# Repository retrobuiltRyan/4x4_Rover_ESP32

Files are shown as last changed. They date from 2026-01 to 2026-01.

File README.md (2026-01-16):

# 4x4_Rover_ESP32
Video is a great overview of capabilites and features.<br>
Watch the video (https://youtu.be/ucYs9Jp9uSM)

gif

Generic platform for 1:10 scale robot rover (skid steer style) with ESP32 and PS4 controller.  Hardware [mostly] from scratch. The 1:10 scale (primarily wheel span and chassis width) mimics some common RC and toy-scale bodies. Makes a uniquie sleeper build that can share a body from off-the-shelf kids toys. PCB has enough functionality to expand into complex robots.
render and real side by side

paa1gcam

PCB can control up to 6 DC motors and 8 Servo Motors. 
PCB render features

## CAD Project (View only) Feel free remix!
[4x4 Rover CAD](https://cad.onshape.com/documents/4f9534eae9bdb33bcf172fe9/w/a4954ea2d6d5d21b33e1d9c4/e/6819e643c891bac21c58d472) (Make a free onShape account to copy and edit)

## 🔩 Mechanical Hardware/Fasteners for Assembly (BoM)
| Item | Assembly | Description | Qty | Cost | Line Total | Vendor Link / McMaster Part# |
|---|---|---|-----|---|---|---|
| 1 | Wheel | Lego "Compatible" Tire 94x38 (or similar)  | 1 | $17.65 | $17.65 | [Link](https://www.aliexpress.us/item/3256808684598937.html) |
| 2 | Drive | Shaft Coupler, 4mm dia | 4 | $1.65  | $6.60 | [Link](https://www.aliexpress.us/item/3256805863207590.html) |
| 3 | Drive | Motor 12V, 82 RPM | 4 | $5.74  | $22.96 | [Link](https://www.aliexpress.us/item/3256807500148966.html) or [Link](https://www.aliexpress.us/item/3256807350691232.html) |
| alt3 | Drive | Motor 12V, 82 RPM + RC Wheel | 4 | $6.46  | $25.84 | [Link](https://www.aliexpress.us/item/3256806026937992.html) |
| 5 | Chassis | #6-32 x 0.5 in Round Head Screw | 28  | $0.03  | $0.94 | 90279A148 |
| 6 | Chassis | #6-32 x 0.75 in Round Head Screw | 20  | $0.04  | $0.83 | 90279A151 |
| 7 | Chassis | #6-32 nut | 20  | $0.02  | $0.40 | 90480A007 |
| 8 | Chassis | #6-32 nylon lock nut | 20  | $0.04  | $0.80 | 99397A622 |
| 9 | Chassis | #6-32 x 1.0 in F/F Hex Standoff (optional) | 4 | $0.47  | $1.88 | 90480A005 |
| 10 | Wheel | #4-40 x 0.5 in Round Head Screw | 16  | $0.02  | $0.32 | 90272A110 |
| 11 | Wheel | #4-40 nut | 16  | $0.01  | $0.16 | 90480A005 |
| 12 | Wheel | #4-40 lock nut (optional) | 16  | $0.03  | $0.48 | 90631A005 |
| 13 | On/Off switch | Switch, SPST | 1 | $0.71  | $0.71 | [Link](https://www.digikey.com/en/products/detail/e-switch/RA11131121/2720267) |
| 14 | 3D Print Parts| PLA Filament (or whatever) | ~650g |$0.02/g | $13 | any | 
| | | | | | **$66.74** | Alternate hardware not included in total cost |

### Optional Forklift Assembly Motors + Parts. *Not a comprehensive list- just the essentials*
| Item | Assembly | Description | Qty | Cost | Line Total | Vendor Link / McMaster Part# |
|---|---|---|-----|---|---|---|
| 15 |Forklift |Motor High Torque 12V, 50RPM, (37mm dia) |  1  | $14 | $14 | [Amazon](https://www.amazon.com/dp/B07K9KPDNV) or [AliExpress](https://www.aliexpress.us/item/2251832401105488.html) |
|16 |Forklift | Flange Coupler 6mm | 1 |$2 | $2 |  [AliExpress](https://www.aliexpress.us/item/3256805863207590.html?) |
| 17 |Forklift |Motor (Linear Actuator ) 12V 50mm-stroke 15mm/s 64N | 2 | $22 | $44 | [AliExpress](https://www.aliexpress.us/item/3256808499012288.html) |
| 18 |Forklift |Bearing 625ZZ , 16mm OD dia, (5x16x5mm) | 8 |$0.55 |$4.40 |[AliExpress](https://www.aliexpress.us/item/3256809469842556.html) |
| 19 |Forklift |Bearing, 11mm OD dia, (5x11x5mm) | 10  | $0.25  | $2.50 | [AliExpress](https://www.aliexpress.us/item/3256807482131308.html) | 

## 🪫 Electronics (Control and Drive PCB)
PS4 Controller (Renewed) https://www.amazon.com/dp/B07QD2HK7B/ref=dp_cr_wdg_tit_rfb  (subject to availability most of the time)
| Reference | Value | Qty | DigiKey P/N | Adafruit P/N | AliExpress | Line total Cost |
|---|---|-----|---|---|---|---|
| BZ1 | Buzzer_5V | 1 | 445-2525-1-ND |  |  | 0.62 |
| C1,C3,C4,C5,C7,C8,C9 | 0.1uF 50V | 7 | 1276-1068-1-ND |  |  | 0.91 |
| C6,C10,C11 | 0.22uF 50V CER | 3 | 445-2283-1-ND |  |  | 0.78 |
| C12,C13,C14 | 22uF 50V | 3 | 399-11438-1-ND |  |  | 1.05 |
| D1,D5,D10,D11 | LED | 4 | 1080-1419-1-ND |  |  | 0.84 |
| D6,D7,D8,D9 | WS2812B | 4 |  | 3094 |  | 0.64 |
| D12 | SMF15A | 1 | SMF15A-E3-08CT-ND |  |  | 0.13 |
| J1 | PINHD_1x2_Male | 1 | S1012EC-40-ND |  |  | 0.43 |
| J2,J12,J14,J16 | Screw_Terminal_4_P3.50mm | 4 | 732-691243110004-ND |  |  | 8.28 |
| J3,J15 | ServoPort_04 | 2 | S1012EC-40-ND |  |  | 0.86 |
| J4,J5,J8,J13 | Screw_Terminal_2_P3.50mm | 4 | 732-2747-ND |  |  | 3.16 |
| J9 | Barrel_Jack | 1 | EJ508A-ND |  |  | 1.22 |
| J17 | PINHD_1x3_Male | 1 |  |  |  | 0 |
| Q1 | MOSFET P-CH 30V 25A TO252 | 1 | 785-1106-1-ND |  |  | 1.43 |
| Q2 | MMBT2222A | 1 | MMBT2222ATPMSCT-ND |  |  | 0.1 |
| Q3 | AO3400A | 1 | 785-1000-1-ND |  |  | 0.46 |
| R1,R2,R4,R7,R8,R9, R10,R13,R18,R22, R36,R37,R38 | 10K | 12 | 311-10.0KFRCT-ND |  |  | 0.14 |
| R3,R6 | 100 | 2 | 311-100FRCT-ND |  |  | 0.2 |
| R5,R19,R20,R32 | 1K | 4 | 311-1.00KFRCT-ND |  |  | 0.44 |
| R16 | 220 | 1 | 311-220FRCT-ND |  |  | 0.1 |
| R17,R21 | 330 | 2 | 311-330FRCT-ND |  |  | 0.22 |
| R33 | 100k | 1 | 311-100KFRCT-ND |  |  | 0.1 |
| RN1,RN2,RN3 | 220 array | 3 | CAY16-201J4LFCT-ND |  |  | 0.3 |
| U1 | INA260 | 1 | 296-47777-1-ND |  |  | 5.52 |
| U2 | ESP32 | 1 | 1965-ESP32-DEVKITC-32UE-ND |  |  | 10 |
| U3 | PCA9685PW | 1 | 568-11925-1-ND |  |  | 3.04 |
| U4,U6,U9 | DRV8833 | 3 |  |  | [Link](https://www.aliexpress.us/item/3256806096142480.html) | 5.23 |
| U5 | UCC27511ADBV | 1 | 296-49474-1-ND |  |  | 1.13 |
| U7 | L7812 | 1 | 296-44522-1-ND |  |  | 1.81 |
| U8 | IMU LSM6DS3TR-C | 1 |  | 4503 |  | 9.95 |
| U14 | MAX40200AUK | 1 | 175-MAX40203AUK+TCT-ND |  |  | 1.75 |
| U15 | L7805 | 1 | 497-7255-1-ND |  |  | 0.84 |
| U18,U19 | MP1584 Buck Module | 2 |  |  | [Link](https://www.aliexpress.us/item/3256806890547813.html) | 1.06 |
| - | PCB | 1 |  |  |  | 1 |
|  |  | |  |  | Total | **$63.74** |

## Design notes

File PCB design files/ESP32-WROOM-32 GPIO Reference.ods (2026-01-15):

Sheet: GPIO Reference
 | ESP32-WROOM-32 GPIO Reference
GPIO | Input | Output | Notes
0 | pulled up | OK | outputs PWM signal at boot, must be LOW to enter flashing mode
1 | TX pin | OK | debug output at boot
2 | OK | OK | connected to on-board LED, must be left floating or LOW to enter flashing mode
3 | OK | RX pin | HIGH at boot
4 | OK | OK
5 | OK | OK | outputs PWM signal at boot, strapping pin
6 | x | x | connected to the integrated SPI flash
7 | x | x | connected to the integrated SPI flash
8 | x | x | connected to the integrated SPI flash
9 | x | x | connected to the integrated SPI flash
10 | x | x | connected to the integrated SPI flash
11 | x | x | connected to the integrated SPI flash
12 | OK | OK | boot fails if pulled high, strapping pin
13 | OK | OK
14 | OK | OK | outputs PWM signal at boot
15 | OK | OK | outputs PWM signal at boot, strapping pin
16 | OK | OK
17 | OK | OK
18 | OK | OK
19 | OK | OK
21 | OK | OK
22 | OK | OK
23 | OK | OK
25 | OK | OK
26 | OK | OK
27 | OK | OK
32 | OK | OK
33 | OK | OK
34 | OK | x | input only
35 | OK | x | input only
36 | OK | x | input only
39 | OK | x | input only

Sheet: IoT Playgnd Pin assignments
 | ESP32-WROOM-32UE GPIO Reference
GPIO | Input | Output | Notes | 4x4 Rover Use | Notes
0 | pulled up | OK | outputs PWM signal at boot, must be LOW to enter flashing mode | enable for 3.3 regulator?
1 | TX pin | OK | debug output at boot | not used
2 | OK | OK | connected to on-board LED, must be left floating or LOW to enter flashing mode | not used
3 | OK | RX pin | HIGH at boot | not used
4 | OK | OK |  | R_MOTOR2_IN2
5 | OK | OK | outputs PWM signal at boot, strapping pin
6 | x | x | connected to the integrated SPI flash | x
7 | x | x | connected to the integrated SPI flash | x
8 | x | x | connected to the integrated SPI flash | x
9 | x | x | connected to the integrated SPI flash | x
10 | x | x | connected to the integrated SPI flash | x
11 | x | x | connected to the integrated SPI flash | x
12 | OK | OK | boot fails if pulled high, strapping pin | not used
13 | OK | OK |  | L_MOTOR1_IN1
14 | OK | OK | outputs PWM signal at boot | not used
15 | OK | OK | outputs PWM signal at boot, strapping pin | not used
16 | OK | OK
17 | OK | OK |  | R_MOTOR2_IN1
18 | OK | OK |  | R_MOTOR1_IN2
19 | OK | OK |  | R_MOTOR1_IN1
21 | OK | OK |  | SDA
22 | OK | OK |  | SCL
23 | OK | OK |  | Buzzer
25 | OK | OK |  | L_MOTOR2_IN2
26 | OK | OK |  | L_MOTOR2_IN1
27 | OK | OK |  | L_MOTOR1_IN2
32 | OK | OK |  | RGB_LED
33 | OK | OK |  | DRV8833 Sleep
34 | OK | x | input only | IR Data
35 | OK | x | input only | Limit A (pullup 10k)
36 | OK | x | input only | Limit B (pullup 10k)
39 | OK | x | input only | not used

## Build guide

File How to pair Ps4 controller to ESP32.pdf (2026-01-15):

Pair PS4 Controller to ESP32-WROOM-32

⭐Goal: Pair a PS4 controller to ESP32 via Bluetooth. This is done in two goals: a) grab the ESP32 MAC address; b) reassign the dualshock4 controller to the ESP32’s MAC address..
📋Requirements:
⚫Genuine Sony Dual Shock 4 Controller.
⚫ESP32 with Bluetooth Classic (BR/EDR) like the ESP32-WROOM-32
⚫PC, USB Cable, Arduino IDE

Note: These newer ESP32 chips do not have Bluetooth Classic, only BLE — so they cannot pair with a PS4 controller (which uses Classic):
❌ESP32-S3 | ✅ESP32-WROOM-32
❌ESP32-C3
❌ESP32-C6
❌ESP32-H2
📄Guide:
1) Upload this code on your ESP32. The serial monitor will output ESP32’s mac address. Document the wifi mac address of the ESP32.

```cpp
#ifdef ESP32

#include <WiFi.h>

#else

#include <ESP8266WiFi.h>

#endif

void setup(){
Serial.begin(115200);
Serial.println();
delay(300);

WiFi.mode(WIFI_STA);//Required to initialize the WiFi hardware on some boards delay(300); //need some time to initialize
Serial.print("ESP Board MAC Address: ");
Serial.println(WiFi.macAddress());

}
void loop(){
}
```

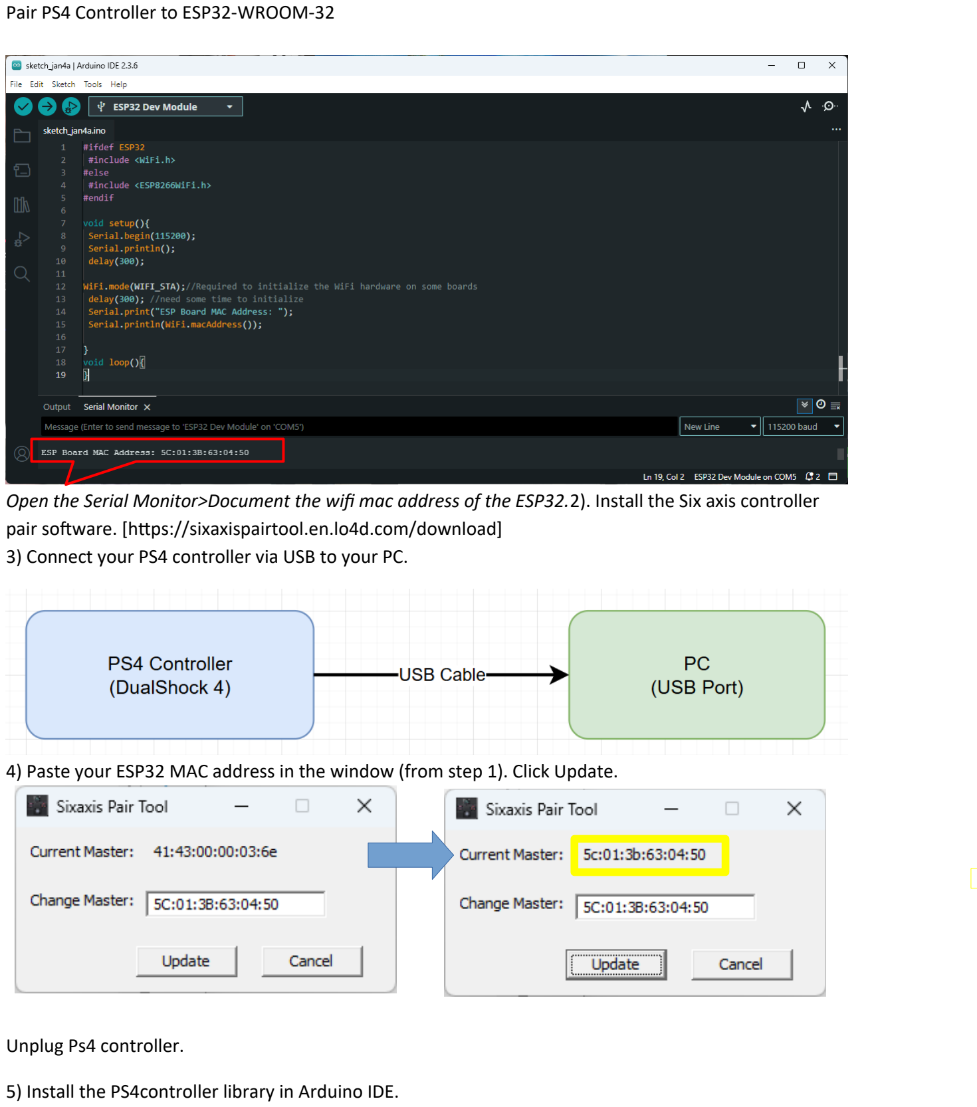
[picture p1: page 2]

Open the Serial Monitor>Document the wifi mac address of the ESP32.2). Install the Six axis controller pair software. [https://sixaxispairtool.en.lo4d.com/download]
3) Connect your PS4 controller via USB to your PC.
4) Paste your ESP32 MAC address in the window (from step 1). Click Update.

Unplug Ps4 controller.

5) Install the PS4controller library in Arduino IDE.

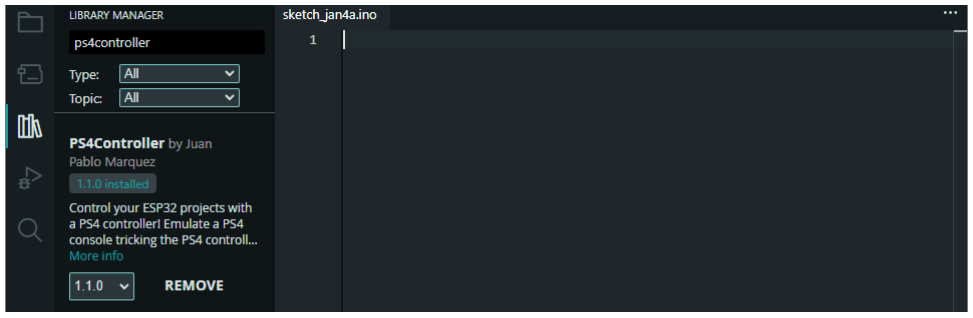
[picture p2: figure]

6) Paste this code into your IDE. Change the MAC address to the one recorded in step 1. Upload this code to your ESP32.

```cpp
#include <PS4Controller.h>

void setup() {
Serial.begin(115200);
//Set ESP32's MAC address to pair with PS4 Controller PS4.begin("xx:xx:xx:xx:xx:xx");//This is your ESP32's MAC !!! Serial.println("Waiting for PS4 controller...");
}

void loop() {
if (PS4.isConnected()) {
Serial.println("Controller connected!"); Serial.print("Battery: "); Serial.println(PS4.Battery()); delay(1000);
}
}
```

Turn on PS4 controller. The controller’s light will change dark blue when connected. The Serial Monitor should show controller is paired.

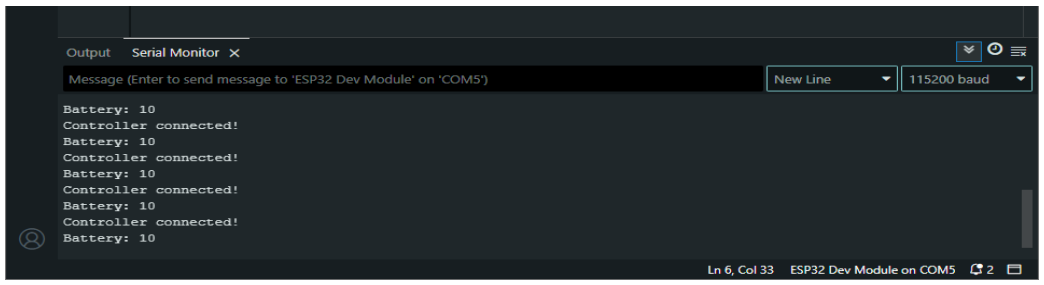
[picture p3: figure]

Done!

## ⚠️Troubleshooting : ⚠️

If you have issues (you paired to something else, controller battery dies) you have to wipe the ESP32’s memory of all paired Bluetooth devices. Wipe the bond pairing data use this sketch:

#include <PS4Controller.h>

#include "esp_bt_main.h"

#include "esp_bt_device.h" #include "esp_gap_bt_api.h" #include "esp_err.h"

void setup()
{
PS4.begin();
uint8_t pairedDeviceBtAddr[20][6];
int count = esp_bt_gap_get_bond_device_num(); esp_bt_gap_get_bond_device_list(&count, pairedDeviceBtAddr); for(int i = 0; i < count; i++)
{
esp_bt_gap_remove_bond_device(pairedDeviceBtAddr[i]);
}
}

void loop()
{
}

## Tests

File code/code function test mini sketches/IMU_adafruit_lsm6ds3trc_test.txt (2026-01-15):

// Basic demo for accelerometer/gyro readings from Adafruit LSM6DS3TR-C
//not exactly sure how to set the poll rate (hz)
#include <Adafruit_LSM6DS3TRC.h>

// For SPI mode, we need a CS pin
#define LSM_CS 10
// For software-SPI mode we need SCK/MOSI/MISO pins
#define LSM_SCK 13
#define LSM_MISO 12
#define LSM_MOSI 11

Adafruit_LSM6DS3TRC lsm6ds3trc;

void setup(void) {
  Serial.begin(115200);

  while (!Serial)
    delay(10); // will pause Zero, Leonardo, etc until serial console opens

  Serial.println("Adafruit LSM6DS3TR-C test!");
  if (!lsm6ds3trc.begin_I2C()) {
    // if (!lsm6ds3trc.begin_SPI(LSM_CS)) {
    // if (!lsm6ds3trc.begin_SPI(LSM_CS, LSM_SCK, LSM_MISO, LSM_MOSI)) {
    Serial.println("Failed to find LSM6DS3TR-C chip");
    while (1) {
      delay(10);
    }
  }

  Serial.println("LSM6DS3TR-C Found!");

  // lsm6ds3trc.setAccelRange(LSM6DS_ACCEL_RANGE_2_G);
  Serial.print("Accelerometer range set to: ");
  switch (lsm6ds3trc.getAccelRange()) {
  case LSM6DS_ACCEL_RANGE_2_G:
    Serial.println("+-2G");
    break;
  case LSM6DS_ACCEL_RANGE_4_G:
    Serial.println("+-4G");
    break;
  case LSM6DS_ACCEL_RANGE_8_G:
    Serial.println("+-8G");
    break;
  case LSM6DS_ACCEL_RANGE_16_G:
    Serial.println("+-16G");
    break;
  }

  // lsm6ds3trc.setGyroRange(LSM6DS_GYRO_RANGE_250_DPS);
  Serial.print("Gyro range set to: ");
  switch (lsm6ds3trc.getGyroRange()) {
  case LSM6DS_GYRO_RANGE_125_DPS:
    Serial.println("125 degrees/s");
    break;
  case LSM6DS_GYRO_RANGE_250_DPS:
    Serial.println("250 degrees/s");
    break;
  case LSM6DS_GYRO_RANGE_500_DPS:
    Serial.println("500 degrees/s");
    break;
  case LSM6DS_GYRO_RANGE_1000_DPS:
    Serial.println("1000 degrees/s");
    break;
  case LSM6DS_GYRO_RANGE_2000_DPS:
    Serial.println("2000 degrees/s");
    break;
  case ISM330DHCX_GYRO_RANGE_4000_DPS:
    break; // unsupported range for the DS33
  }

  // lsm6ds3trc.setAccelDataRate(LSM6DS_RATE_12_5_HZ);
  Serial.print("Accelerometer data rate set to: ");
  switch (lsm6ds3trc.getAccelDataRate()) {
  case LSM6DS_RATE_SHUTDOWN:
    Serial.println("0 Hz");
    break;
  case LSM6DS_RATE_12_5_HZ:
    Serial.println("12.5 Hz");
    break;
  case LSM6DS_RATE_26_HZ:
    Serial.println("26 Hz");
    break;
  case LSM6DS_RATE_52_HZ:
    Serial.println("52 Hz");
    break;
  // case LSM6DS_RATE_104_HZ:
  //   Serial.println("104 Hz");
  //   break;
  // case LSM6DS_RATE_208_HZ:
  //   Serial.println("208 Hz");
  //   break;
  // case LSM6DS_RATE_416_HZ:
  //   Serial.println("416 Hz");
  //   break;
  // case LSM6DS_RATE_833_HZ:
  //   Serial.println("833 Hz");
  //   break;
  // case LSM6DS_RATE_1_66K_HZ:
  //   Serial.println("1.66 KHz");
  //   break;
  // case LSM6DS_RATE_3_33K_HZ:
  //   Serial.println("3.33 KHz");
  //   break;
  // case LSM6DS_RATE_6_66K_HZ:
  //   Serial.println("6.66 KHz");
  //   break;
  }

  // lsm6ds3trc.setGyroDataRate(LSM6DS_RATE_12_5_HZ);
  Serial.print("Gyro data rate set to: ");
  switch (lsm6ds3trc.getGyroDataRate()) {
  case LSM6DS_RATE_SHUTDOWN:
    Serial.println("0 Hz");
    break;
  case LSM6DS_RATE_12_5_HZ:
    Serial.println("12.5 Hz");
    break;
  case LSM6DS_RATE_26_HZ:
    Serial.println("26 Hz");
    break;
  case LSM6DS_RATE_52_HZ:
    Serial.println("52 Hz");
    break;
  // case LSM6DS_RATE_104_HZ:
  //   Serial.println("104 Hz");
  //   break;
  // case LSM6DS_RATE_208_HZ:
  //   Serial.println("208 Hz");
  //   break;
  // case LSM6DS_RATE_416_HZ:
  //   Serial.println("416 Hz");
  //   break;
  // case LSM6DS_RATE_833_HZ:
  //   Serial.println("833 Hz");
  //   break;
  // case LSM6DS_RATE_1_66K_HZ:
  //   Serial.println("1.66 KHz");
  //   break;
  // case LSM6DS_RATE_3_33K_HZ:
  //   Serial.println("3.33 KHz");
  //   break;
  // case LSM6DS_RATE_6_66K_HZ:
  //   Serial.println("6.66 KHz");
  //   break;
  }

  lsm6ds3trc.configInt1(false, false, true); // accelerometer DRDY on INT1
  lsm6ds3trc.configInt2(false, true, false); // gyro DRDY on INT2
}

void loop() {
  // Get a new normalized sensor event
  sensors_event_t accel;
  sensors_event_t gyro;
  sensors_event_t temp;
  lsm6ds3trc.getEvent(&accel, &gyro, &temp);

  Serial.print("\t\tTemperature ");
  Serial.print(temp.temperature);
  Serial.println(" deg C");

  /* Display the results (acceleration is measured in m/s^2) */
  Serial.print("\t\tAccel X: ");
  Serial.print(accel.acceleration.x);
  Serial.print(" \tY: ");
  Serial.print(accel.acceleration.y);
  Serial.print(" \tZ: ");
  Serial.print(accel.acceleration.z);
  Serial.println(" m/s^2 ");

  /* Display the results (rotation is measured in rad/s) */
  Serial.print("\t\tGyro X: ");
  Serial.print(gyro.gyro.x);
  Serial.print(" \tY: ");
  Serial.print(gyro.gyro.y);
  Serial.print(" \tZ: ");
  Serial.print(gyro.gyro.z);
  Serial.println(" radians/s ");
  Serial.println();

  delay(100);

  //  // serial plotter friendly format

  //  Serial.print(temp.temperature);
  //  Serial.print(",");

  //  Serial.print(accel.acceleration.x);
  //  Serial.print(","); Serial.print(accel.acceleration.y);
  //  Serial.print(","); Serial.print(accel.acceleration.z);
  //  Serial.print(",");

  // Serial.print(gyro.gyro.x);
  // Serial.print(","); Serial.print(gyro.gyro.y);
  // Serial.print(","); Serial.print(gyro.gyro.z);
  // Serial.println();
  //  delayMicroseconds(10000);
}

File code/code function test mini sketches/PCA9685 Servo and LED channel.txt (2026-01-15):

#include <Wire.h>
#include <Adafruit_PWMServoDriver.h>

// Create PCA9685 object
Adafruit_PWMServoDriver pwm = Adafruit_PWMServoDriver();

// Servo config for SG90
#define SERVO_CHANNEL 0   // Channel 0 on PCA9685
#define SERVO_MIN 160     // ~500 µs pulse for 0° 150-600 is 0 - 180 range. Shorten if servo 
#define SERVO_MAX 590     // ~2400 µs pulse for 180°

// DRV8833 motor control pins on PCA9685
#define MOTOR_IN1_CHANNEL 8
#define MOTOR_IN2_CHANNEL 9

#define SLEEP_PIN 33

void setup() {
  Serial.begin(115200);
  Serial.println("PCA9685 SG90 Servo Test");

  pinMode(SLEEP_PIN, OUTPUT);
  digitalWrite(SLEEP_PIN, LOW); // disable the DRV8833 drivers for this demo

  pwm.begin();
  pwm.setPWMFreq(50);  // SG90 expects ~50 Hz

  delay(20);
}

// Convert angle (0-180) to pulse length
uint16_t angleToPulse(int angle) {
  return map(angle, 0, 180, SERVO_MIN, SERVO_MAX);
}

void loop() {

// setPWM(channel, onStep, offStep):
//   channel  -> which PCA9685 output (0–15)
//   onStep   -> 0–4095 tick count when signal goes HIGH
//   offStep  -> 0–4095 tick count when signal goes LOW
// Example: setPWM(0, 0, 300) → on channel 0, pulse starts at step 0 and ends at step 300

//Go to Angle Commands and rest
pwm.setPWM(SERVO_CHANNEL, 0, angleToPulse(10)); //mechanical limit is around 0
delay(1500);

pwm.setPWM(SERVO_CHANNEL, 0, angleToPulse(45));
delay(1500);

pwm.setPWM(SERVO_CHANNEL, 0, angleToPulse(90)); //Using a SG90, range beyond 90deg will break something
delay(1500);

//pwm.setPWM(SERVO_CHANNEL, 0, angleToPulse(135));
delay(1500);

//pwm.setPWM(SERVO_CHANNEL, 0, angleToPulse(170)); //mechanical limit is around 180
delay(1500);

 // Sweep duty cycle UP// LEDs will flicker is the PWM Freq is low (50Hz is used in this example)
  for (int duty = 0; duty <= 4095; duty += 25) {
    pwm.setPWM(12, 0, duty);  // duty ranges 0..4095 (~0..100%)
    delay(10);
  }

  delay(500);

  // Sweep duty cycle DOWN
  for (int duty = 4095; duty >= 0; duty -= 25) {
    pwm.setPWM(12, 0, duty);
    delay(10);
  }

  delay(500);

// Turn channel 12 fully ON
pwm.setPWM(12, 4096, 0);
Serial.println("Ch12 ON");
delay(1000);
// Turn channel 12 fully OFF
pwm.setPWM(12, 0, 0);
Serial.println("Ch12 OFF");
delay(1000);

  // Sweep with angle commands
  for (int angle = 0; angle <= 90; angle += 5) {
    pwm.setPWM(SERVO_CHANNEL, 0, angleToPulse(angle));
    delay(50);
  }

  delay(500);

  for (int angle = 90; angle >= 0; angle -= 5) {
    pwm.setPWM(SERVO_CHANNEL, 0, angleToPulse(angle));
    delay(50);
  }

  delay(500);

  // Test motor forward/reverse :Drive the DRV8833 with the PCA9865 CH8 and CH9
  testMotor();
}
//=====================subroutines==================================================
// 🔁 Function to test DC motor forward and reverse
void testMotor() {
  digitalWrite(SLEEP_PIN, HIGH); //enable the DRV8833 driver
  Serial.println("Motor Forward");
  // IN1 = HIGH, IN2 = LOW → Forward
  pwm.setPWM(MOTOR_IN1_CHANNEL, 4096, 0); // Fully ON
  pwm.setPWM(MOTOR_IN2_CHANNEL, 0, 0);    // Fully OFF
  delay(1000);

  Serial.println("Motor Stop");
  // Brake/stop: both LOW (or both HIGH)
  pwm.setPWM(MOTOR_IN1_CHANNEL, 0, 0);
  pwm.setPWM(MOTOR_IN2_CHANNEL, 0, 0);
  delay(500);

  Serial.println("Motor Reverse");
  // IN1 = LOW, IN2 = HIGH → Reverse
  pwm.setPWM(MOTOR_IN1_CHANNEL, 0, 0);
  pwm.setPWM(MOTOR_IN2_CHANNEL, 4096, 0);
  delay(1000);

  Serial.println("Motor Stop");
  pwm.setPWM(MOTOR_IN1_CHANNEL, 0, 0);
  pwm.setPWM(MOTOR_IN2_CHANNEL, 0, 0);
  delay(1000);

   digitalWrite(SLEEP_PIN, LOW); //disable the DRV8833 driver
}

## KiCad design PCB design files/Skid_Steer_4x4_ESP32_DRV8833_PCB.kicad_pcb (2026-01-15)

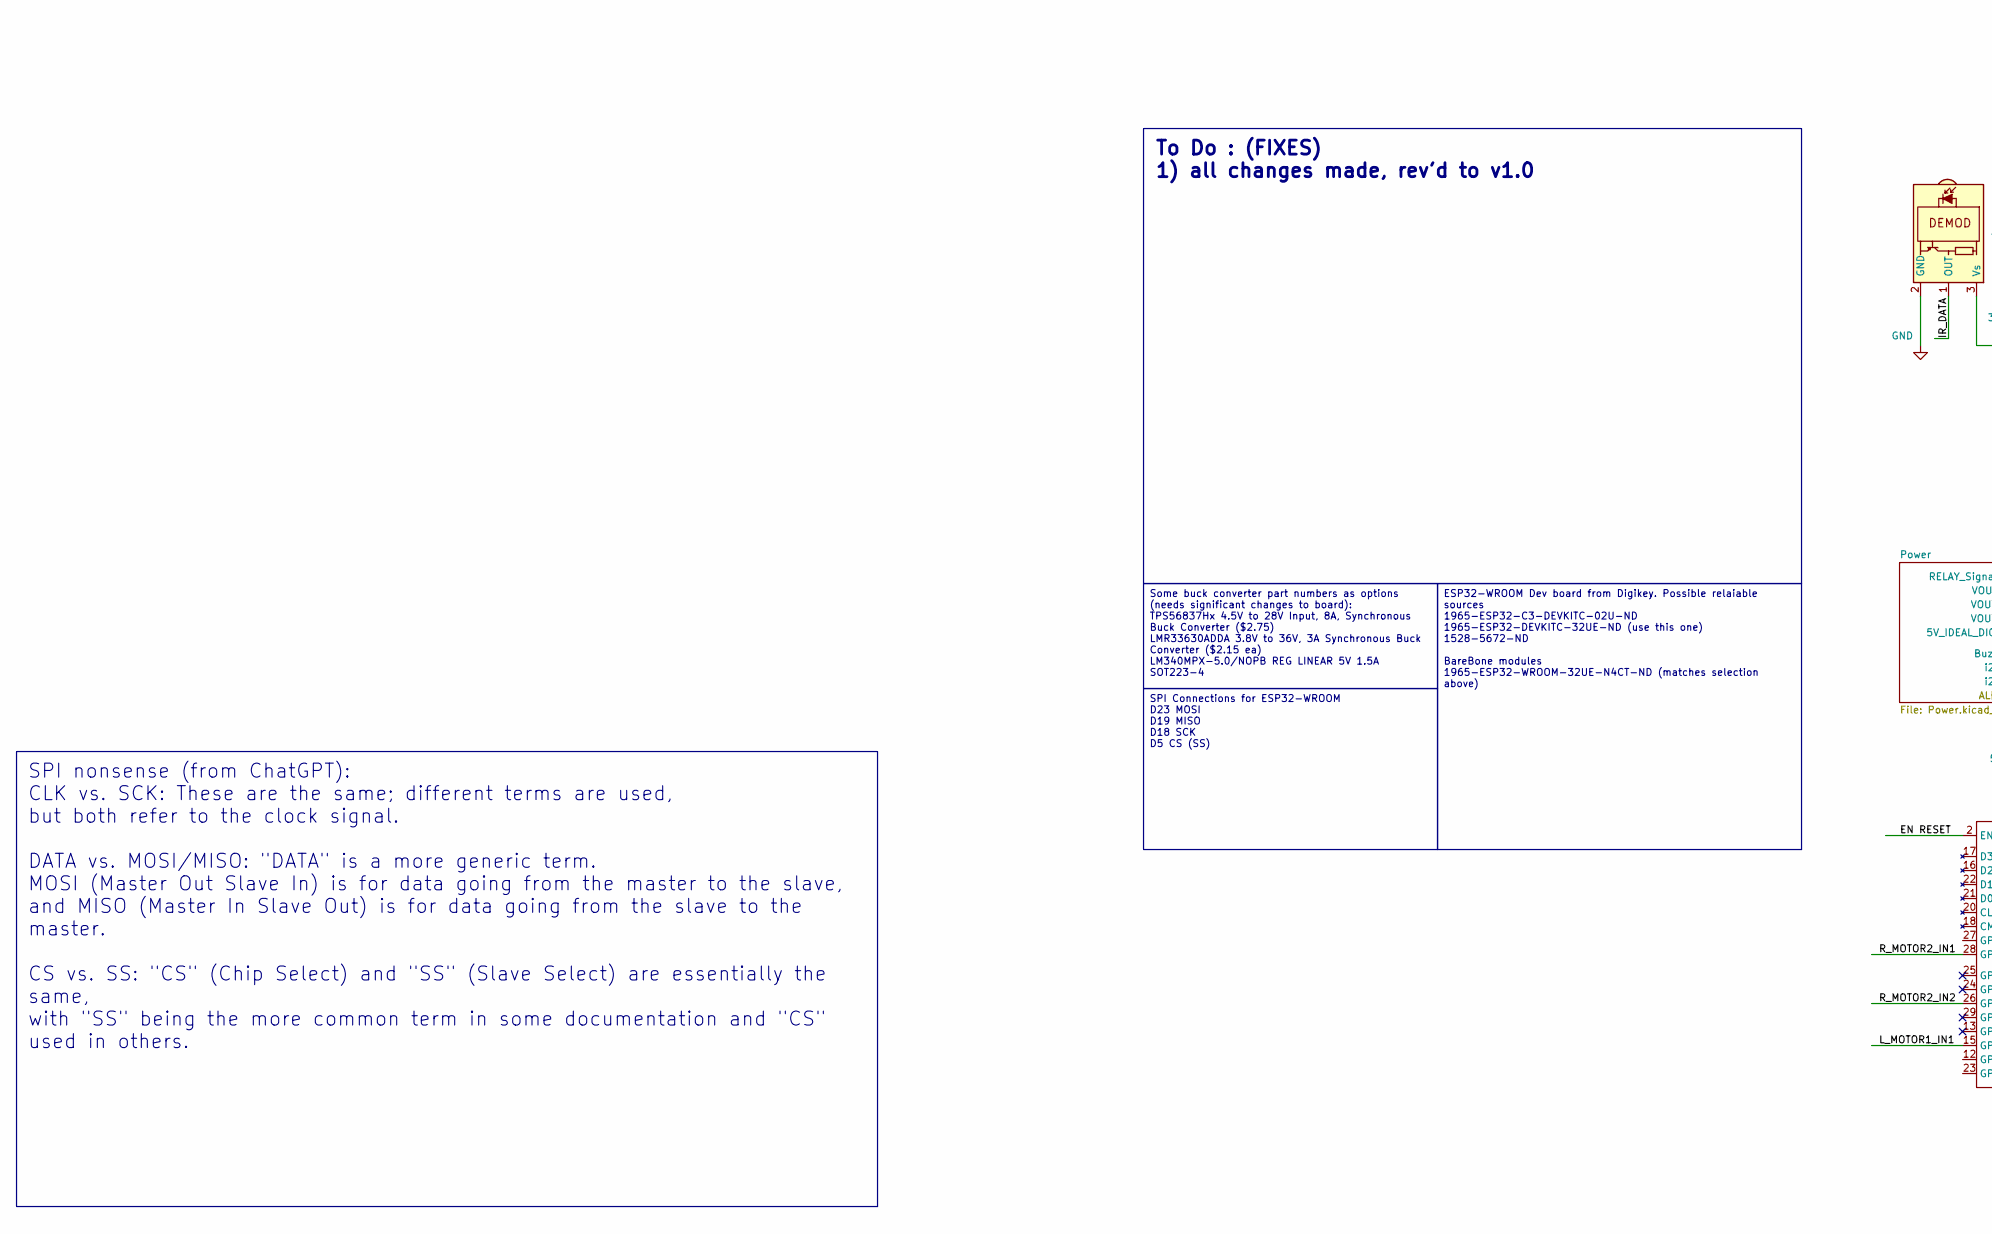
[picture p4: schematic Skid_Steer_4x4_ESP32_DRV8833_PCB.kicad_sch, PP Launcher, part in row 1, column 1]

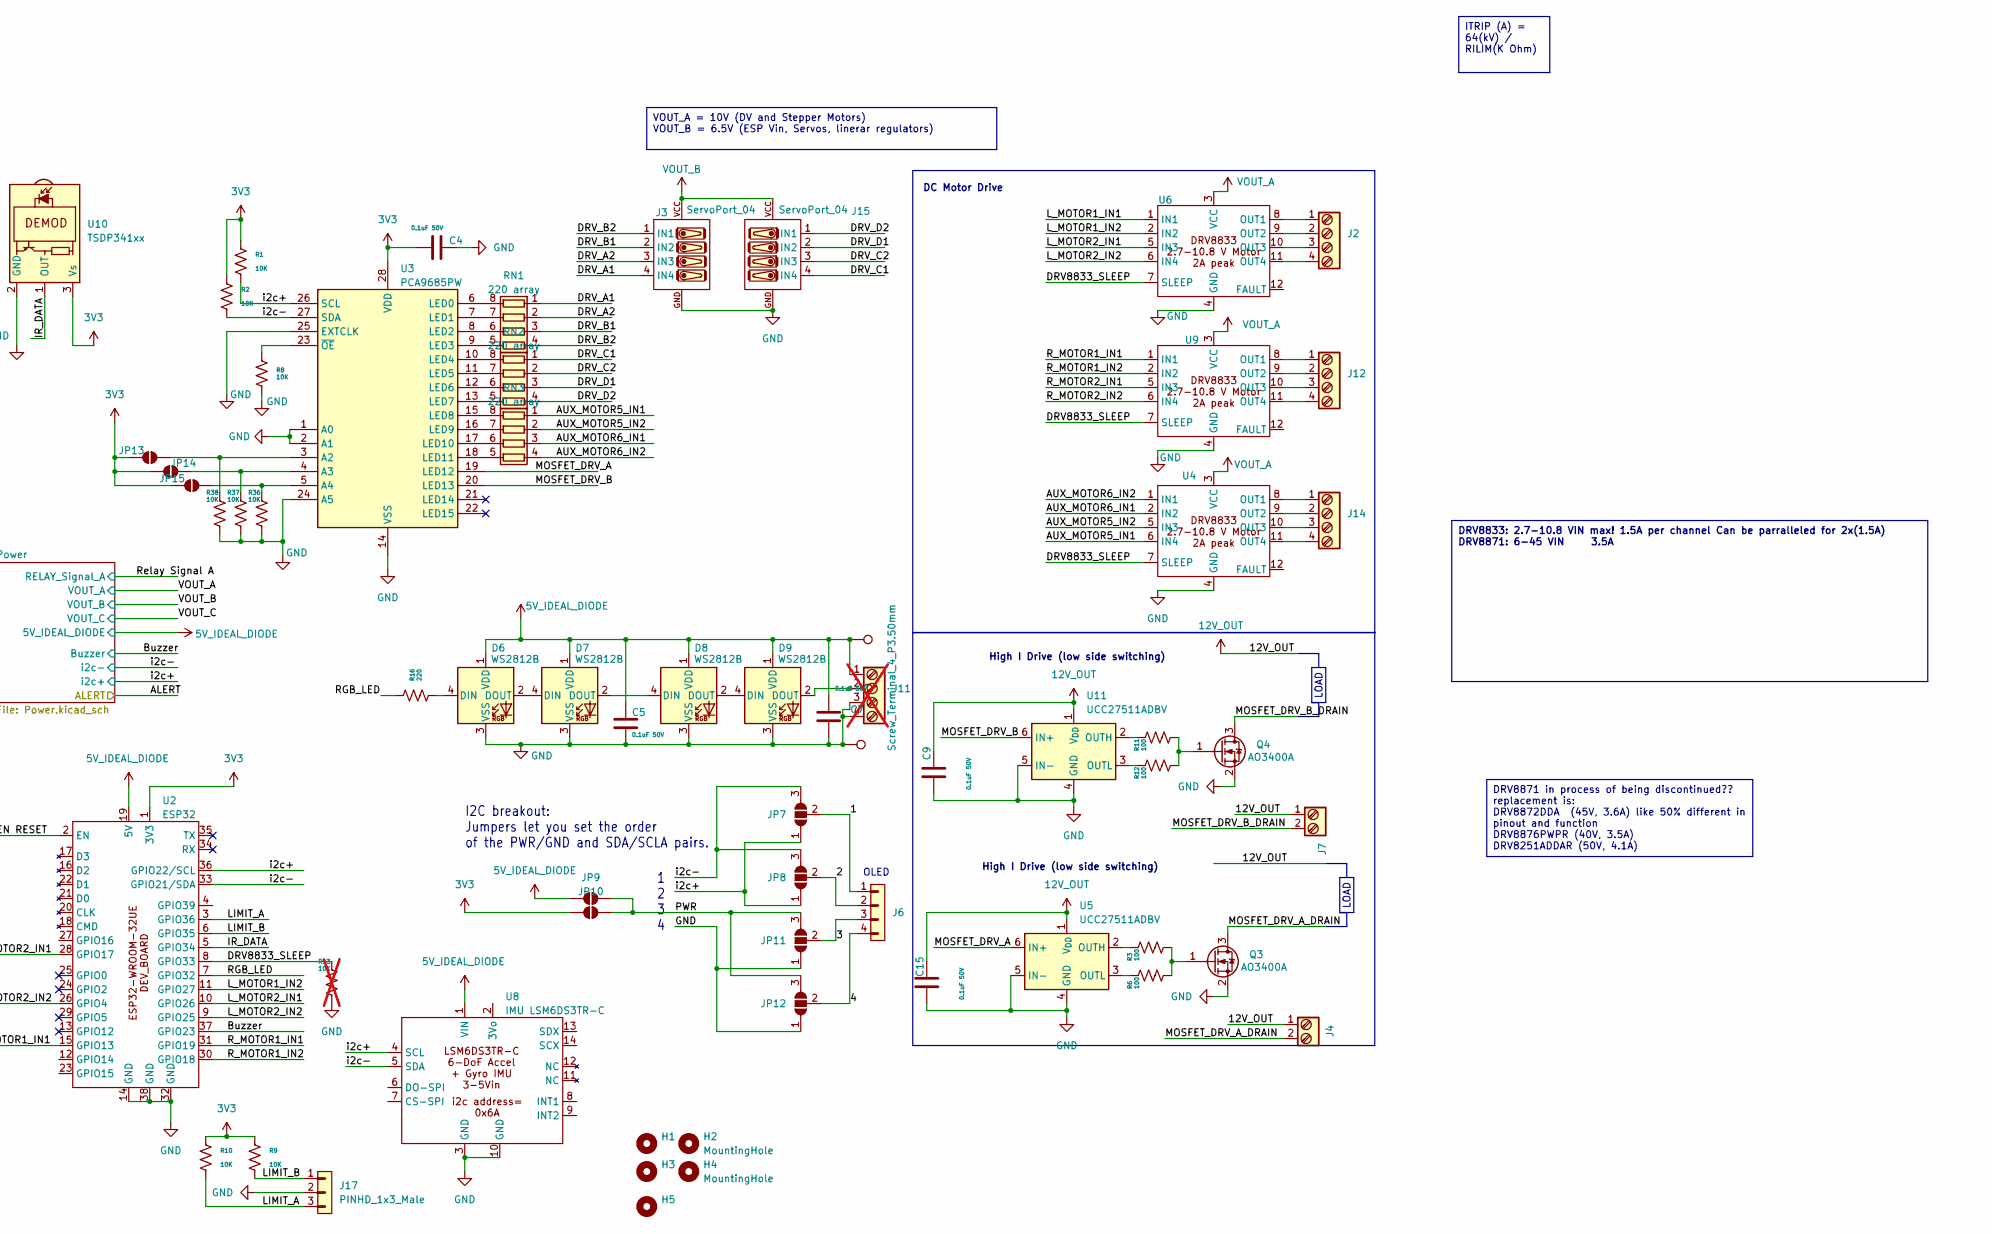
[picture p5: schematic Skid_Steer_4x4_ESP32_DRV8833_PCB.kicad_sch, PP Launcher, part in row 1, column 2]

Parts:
C4, C5, C7, C9, C15: 0.1uF 50V; C_1206_3216Metric; DigiKey P/N 1276-1068-1-ND
D6, D7, D8, D9: WS2812B; LED_WS2812B_PLCC4_5.0x5.0mm_P3.2mm
H1, H2, H3, H4, H5: MountingHole; MountingHole_4.3mm_M4
J2, J12, J14: Screw_Terminal_4_P3.50mm; TerminalBlock_Phoenix_PT-1,5-4-3.5-H_1x04_P3.50mm_Horizontal; DigiKey P/N 732-691243110004-ND
J3, J15: ServoPort_04; ServoPort_04_Vertical; DigiKey P/N S1012EC-40-ND
J4, J7: Screw_Terminal_2_P3.50mm; TerminalBlock_Phoenix_PT-1,5-2-3.5-H_1x02_P3.50mm_Horizontal; DigiKey P/N 732-2747-ND
J6: PINHD_1x4_Male; PinHeader_1x04_P2.54mm_Vertical; DigiKey P/N S1012EC-40-ND
J11: Screw_Terminal_4_P3.50mm; TerminalBlock_Phoenix_PT-1,5-4-3.5-H_1x04_P3.50mm_Horizontal; not fitted
J17: PINHD_1x3_Male; PinHeader_1x03_P2.54mm_Vertical
JP7, JP8, JP11, JP12: SolderJumper_3_Open; SolderJumper-3_P1.3mm_Open_RoundedPad1.0x1.5mm
JP9, JP10, JP13, JP14, JP15: SolderJumper_2_Open; SolderJumper-2_P1.3mm_Open_TrianglePad1.0x1.5mm
Q3, Q4: AO3400A; SOT-23-3; DigiKey P/N 785-1000-1-ND
R1, R2, R8, R9, R10, R36, R37, R38: 10K; R_1206_3216Metric; DigiKey P/N 311-10.0KFRCT-ND
R3, R6, R11, R12: 100; R_1206_3216Metric; DigiKey P/N 311-100FRCT-ND
R13: 10K; R_1206_3216Metric; DigiKey P/N 311-10.0KFRCT-ND; not fitted
R16: 220; R_1206_3216Metric; DigiKey P/N 311-220FRCT-ND
RN1, RN2, RN3: 220 array; CAT16-4_R-Array_1206; DigiKey P/N CAY16-201J4LFCT-ND
TP4, TP5, TP6: TestPoint; TestPoint_Pad_1.5x1.5mm
U2: ESP32; ESP32-WROOM-32UE_DEV_BOARD; DigiKey P/N 1965-ESP32-DEVKITC-32UE-ND
U3: PCA9685PW; TSSOP-28_4.4x9.7mm_P0.65mm; DigiKey P/N 568-11925-1-ND
U4, U6, U9: DRV8833; DRV8833_aliexpress
U5, U11: UCC27511ADBV; SOT-23-6; DigiKey P/N 296-49474-1-ND
U8: IMU LSM6DS3TR-C; LSM6DS3TR-C_Adafruit
U10: TSDP341xx; Vishay_MOLD-3Pin

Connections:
3V3: C4.1, JP10.1 (A), JP13.1 (A), JP14.1 (A), JP15.1 (A), R1.2, R2.2, R9.2, R10.2, U2.1 (3V3), U3.28 (VDD), U10.3 (Vs); also elsewhere on the board
5V_IDEAL_DIODE: C5.1, C7.1, D6.1 (VDD), D7.1 (VDD), D8.1 (VDD), D9.1 (VDD), J11.1, JP9.1 (A), TP5.1, U2.19 (5V), U8.1 (VIN); also elsewhere on the board
12V_OUT: C9.2, C15.2, J4.1, J7.1, U5.1 (V_{DD}), U11.1 (V_{DD}); also elsewhere on the board
/1: J6.1, JP7.2 (C)
/2: J6.2, JP8.2 (C)
/3: J6.3, JP11.2 (C)
/4: J6.4, JP12.2 (C)
/AUX_MOTOR5_IN1: RN3.1 (R1.1), U4.6 (IN4)
/AUX_MOTOR5_IN2: RN3.2 (R2.1), U4.5 (IN3)
/AUX_MOTOR6_IN1: RN3.3 (R3.1), U4.2 (IN2)
/AUX_MOTOR6_IN2: RN3.4 (R4.1), U4.1 (IN1)
/Buzzer: U2.37 (GPIO23); also elsewhere on the board
/DRV8833_SLEEP: R13.1, U2.8 (GPIO33), U4.7 (SLEEP), U6.7 (SLEEP), U9.7 (SLEEP)
/DRV_A1: J3.4 (IN4), RN1.1 (R1.1)
/DRV_A2: J3.3 (IN3), RN1.2 (R2.1)
/DRV_B1: J3.2 (IN2), RN1.3 (R3.1)
/DRV_B2: J3.1 (IN1), RN1.4 (R4.1)
/DRV_C1: J15.4 (IN4), RN2.1 (R1.1)
/DRV_C2: J15.3 (IN3), RN2.2 (R2.1)
/DRV_D1: J15.2 (IN2), RN2.3 (R3.1)
/DRV_D2: J15.1 (IN1), RN2.4 (R4.1)
/EN RESET: U2.2 (EN)
/IR_DATA: U2.5 (GPIO34), U10.1 (OUT)
/LIMIT_A: J17.3, R10.1, U2.3 (GPIO36)
/LIMIT_B: J17.1, R9.1, U2.6 (GPIO35)
/L_MOTOR1_IN1: U2.15 (GPIO13), U6.1 (IN1)
/L_MOTOR1_IN2: U2.11 (GPIO27), U6.2 (IN2)
/L_MOTOR2_IN1: U2.10 (GPIO26), U6.5 (IN3)
/L_MOTOR2_IN2: U2.9 (GPIO25), U6.6 (IN4)
/MOSFET_DRV_A: U3.19 (LED12), U5.6 (IN+)
/MOSFET_DRV_A_DRAIN: J4.2, Q3.3 (D)
/MOSFET_DRV_B: U3.20 (LED13), U11.6 (IN+)
/MOSFET_DRV_B_DRAIN: J7.2, Q4.3 (D)
/PWR: JP9.2 (B), JP10.2 (B), JP11.3 (B), JP12.3 (B)
/RGB_LED: R16.2, U2.7 (GPIO32)
/R_MOTOR1_IN1: U2.31 (GPIO19), U9.1 (IN1)
/R_MOTOR1_IN2: U2.30 (GPIO18), U9.2 (IN2)
/R_MOTOR2_IN1: U2.28 (GPIO17), U9.5 (IN3)
/R_MOTOR2_IN2: U2.26 (GPIO4), U9.6 (IN4)
/i2c+: JP7.1 (A), JP8.1 (A), R1.1, U2.36 (GPIO22/SCL), U3.26 (SCL), U8.4 (SCL); also elsewhere on the board
/i2c-: JP7.3 (B), JP8.3 (B), R2.1, U2.33 (GPIO21/SDA), U3.27 (SDA), U8.5 (SDA); also elsewhere on the board
GND: C4.2, C5.2, C7.2, C9.1, C15.1, D6.3 (VSS), D7.3 (VSS), D8.3 (VSS), D9.3 (VSS), J3.GND, J11.3, J11.4, J15.GND, J17.2, JP11.1 (A), JP12.1 (A), Q3.2 (S), Q4.2 (S), R8.2, R13.2, R36.2, R37.2, R38.2, TP6.1, U2.14 (GND), U2.32 (GND), U2.38 (GND), U3.1 (A0), U3.2 (A1), U3.14 (VSS), U3.24 (A5), U3.25 (EXTCLK), U4.4 (GND), U5.4 (GND), U5.5 (IN-), U6.4 (GND), U8.3 (GND), U8.10 (GND), U9.4 (GND), U10.2 (GND), U11.4 (GND), U11.5 (IN-); also elsewhere on the board
unnamed: D6.4 (DIN), R16.1
unnamed: D6.2 (DOUT), D7.4 (DIN)
unnamed: D7.2 (DOUT), D8.4 (DIN)
unnamed: D8.2 (DOUT), D9.4 (DIN)
unnamed: D9.2 (DOUT), J11.2, TP4.1
unnamed: JP13.2 (B), R38.1, U3.3 (A2)
unnamed: JP14.2 (B), R37.1, U3.4 (A3)
unnamed: JP15.2 (B), R36.1, U3.5 (A4)
unnamed: Q3.1 (G), R3.2, R6.2
unnamed: Q4.1 (G), R11.2, R12.2
unnamed: RN1.8 (R1.2), U3.6 (LED0)
unnamed: RN1.7 (R2.2), U3.7 (LED1)
unnamed: RN1.6 (R3.2), U3.8 (LED2)
unnamed: RN1.5 (R4.2), U3.9 (LED3)
unnamed: RN2.8 (R1.2), U3.10 (LED4)
unnamed: RN2.7 (R2.2), U3.11 (LED5)
unnamed: RN2.6 (R3.2), U3.12 (LED6)
unnamed: RN2.5 (R4.2), U3.13 (LED7)
unnamed: RN3.8 (R1.2), U3.15 (LED8)
unnamed: RN3.7 (R2.2), U3.16 (LED9)
unnamed: RN3.6 (R3.2), U3.17 (LED10)
unnamed: RN3.5 (R4.2), U3.18 (LED11)
unnamed: R8.1, U3.23 (~OE)
unnamed: J14.1, U4.8 (OUT1)
unnamed: J14.2, U4.9 (OUT2)
unnamed: J14.3, U4.10 (OUT3)
unnamed: J14.4, U4.11 (OUT4)
unnamed: R3.1, U5.2 (OUTH)
unnamed: R6.1, U5.3 (OUTL)
unnamed: J2.1, U6.8 (OUT1)
unnamed: J2.2, U6.9 (OUT2)
unnamed: J2.3, U6.10 (OUT3)
unnamed: J2.4, U6.11 (OUT4)
unnamed: J12.1, U9.8 (OUT1)
unnamed: J12.2, U9.9 (OUT2)
unnamed: J12.3, U9.10 (OUT3)
unnamed: J12.4, U9.11 (OUT4)
unnamed: R11.1, U11.2 (OUTH)
unnamed: R12.1, U11.3 (OUTL)
VOUT_A: U4.3 (VCC), U6.3 (VCC), U9.3 (VCC); also elsewhere on the board
VOUT_B: J3.VCC, J15.VCC; also elsewhere on the board

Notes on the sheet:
VOUT_A = 10V (DV and Stepper Motors) VOUT_B = 6.5V (ESP Vin, Servos, linerar regulators)
LOAD
SPI Connections for ESP32-WROOM D23 MOSI D19 MISO D18 SCK D5 CS (SS)
SPI nonsense (from ChatGPT): CLK vs. SCK: These are the same; different terms are used, but both refer to the clock signal. DATA vs. MOSI/MISO: "DATA" is a more generic term. MOSI (Master Out Slave In) is for data going from the master to the slave, and MISO (Master In Slave Out) is for data going 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
Some buck converter part numbers as options (needs significant changes to board): TPS56837Hx 4.5V to 28V Input, 8A, Synchronous Buck Converter ($2.75) LMR33630ADDA 3.8V to 36V, 3A Synchronous Buck Converter ($2.15 ea) LM340MPX-5.0/NOPB REG LINEAR 5V 1.5A SOT223-4
To Do : (FIXES) 1) all changes made, rev'd to v1.0
ITRIP (A) = 64(kV) / RILIM(K Ohm)
ESP32-WROOM Dev board from Digikey. Possible relaiable sources 1965-ESP32-C3-DEVKITC-02U-ND 1965-ESP32-DEVKITC-32UE-ND (use this one) 1528-5672-ND BareBone modules 1965-ESP32-WROOM-32UE-N4CT-ND (matches selection above)
DRV8871 in process of being discontinued?? replacement is: DRV8872DDA (45V, 3.6A) like 50% different in pinout and function DRV8876PWPR (40V, 3.5A) DRV8251ADDAR (50V, 4.1A)
DRV8833: 2.7-10.8 VIN max! 1.5A per channel Can be parralleled for 2x(1.5A) DRV8871: 6-45 VIN 3.5A
DC Motor Drive
1 2 3 4
I2C breakout: Jumpers let you set the order of the PWR/GND and SDA/SCLA pairs.
High I Drive (low side switching)
OLED

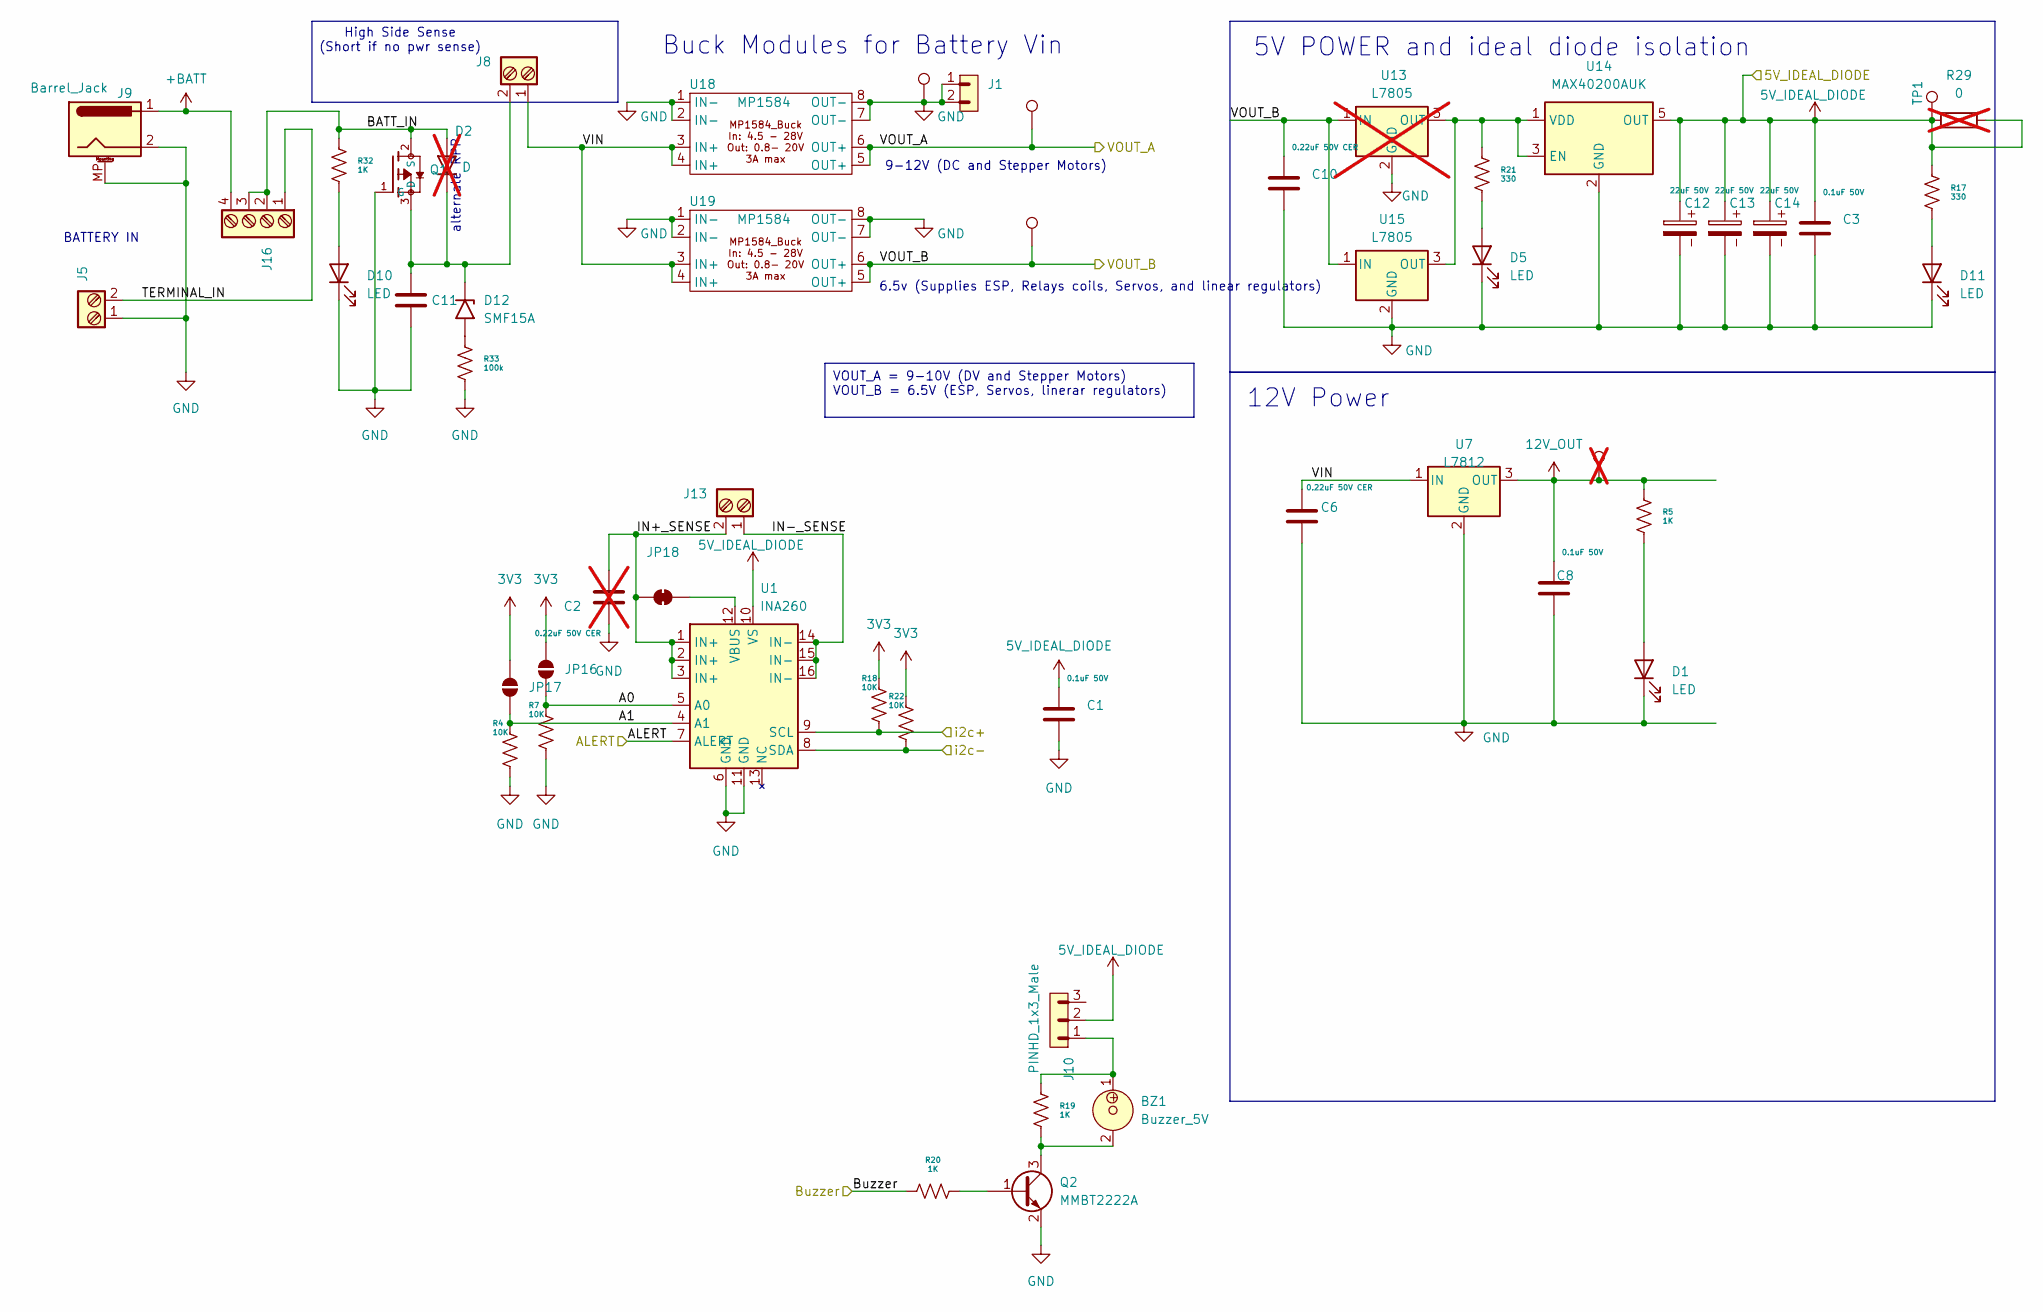
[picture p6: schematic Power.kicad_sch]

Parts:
BZ1: Buzzer_5V; MagneticBuzzer_ProSignal_ABT-410-RC; DigiKey P/N 445-2525-1-ND
C1, C3, C8: 0.1uF 50V; C_1206_3216Metric; DigiKey P/N 1276-1068-1-ND
C2: 0.22uF 50V CER; C_1206_3216Metric; DigiKey P/N 445-2283-1-ND; not fitted
C6, C10, C11: 0.22uF 50V CER; C_1206_3216Metric; DigiKey P/N 445-2283-1-ND
C12, C13, C14: 22uF 50V; CP_Elec_5x5.3; DigiKey P/N 399-11438-1-ND
D1, D5, D10, D11: LED; LED_1206_3216Metric; DigiKey P/N 1080-1419-1-ND
D2: D; D_SMC_Handsoldering; DigiKey P/N S5AC-FDICT-ND; not fitted
D12: SMF15A; D_SMF; DigiKey P/N SMF15A-E3-08CT-ND
J1: PINHD_1x2_Male; PinHeader_1x02_P2.54mm_Vertical; DigiKey P/N S1012EC-40-ND
J5, J8, J13: Screw_Terminal_2_P3.50mm; TerminalBlock_Phoenix_PT-1,5-2-3.5-H_1x02_P3.50mm_Horizontal; DigiKey P/N 732-2747-ND
J9: Barrel_Jack; BarrelJack_GCT_DCJ200-10-A_Horizontal; DigiKey P/N EJ508A-ND
J10: PINHD_1x3_Male; PinHeader_1x03_P2.54mm_Vertical; DigiKey P/N S1012EC-40-ND
J16: Screw_Terminal_4_P3.50mm; TerminalBlock_Phoenix_PT-1,5-4-3.5-H_1x04_P3.50mm_Horizontal; DigiKey P/N 732-691243110004-ND
JP16, JP17: SolderJumper_2_Open; SolderJumper-2_P1.3mm_Open_TrianglePad1.0x1.5mm
JP18: SolderJumper_2_Bridged; SolderJumper-2_P1.3mm_Bridged_RoundedPad1.0x1.5mm
Q1: MOSFET P-CH 30V 25A TO252; MOSFET_P-CH_30V_25A_TO252; DigiKey P/N 785-1106-1-ND
Q2: MMBT2222A; SOT-23; DigiKey P/N MMBT2222ATPMSCT-ND
R4, R7, R18, R22: 10K; R_1206_3216Metric; DigiKey P/N 311-10.0KFRCT-ND
R5, R19, R20, R32: 1K; R_1206_3216Metric; DigiKey P/N 311-1.00KFRCT-ND
R17, R21: 330; R_1206_3216Metric; DigiKey P/N 311-330FRCT-ND
R29: 0; R_2512_6332Metric_Pad1.40x3.35mm_HandSolder; DigiKey P/N YAG1232CT-ND; not fitted
R33: 100k; R_1206_3216Metric; DigiKey P/N 311-100KFRCT-ND
TP1: TestPoint; TestPoint_Pad_2.0x2.0mm
TP2: uC +5V; TestPoint_Pad_2.0x2.0mm; not fitted
TP10, TP11, TP12: TestPoint; TestPoint_Pad_1.5x1.5mm
U1: INA260; TSSOP-16_4.4x5mm_P0.65mm; DigiKey P/N 296-47777-1-ND
U7: L7812; TO-263-3_TabPin2; DigiKey P/N 296-44522-1-ND
U13: L7805; TO-220-3_Vertical; not fitted
U14: MAX40200AUK; SOT-23-5; DigiKey P/N 175-MAX40203AUK+TCT-ND
U15: L7805; TO-252-2; DigiKey P/N 497-7255-1-ND
U18, U19: MP1584

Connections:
3V3: JP16.2 (B), JP17.2 (B), R18.1, R22.1; also elsewhere on the board
5V_IDEAL_DIODE: C1.1, C3.1, C12.1, C13.1, C14.1, J10.2, R17.1, R29.1, R29.2, TP1.1, U1.10 (VS), U14.5 (OUT); also elsewhere on the board
12V_OUT: C8.1, R5.2, TP2.1, U7.3 (OUT); also elsewhere on the board
+BATT: J9.1, J16.4
/Buzzer: R20.1; also elsewhere on the board
/Power/A0: JP16.1 (A), R7.1, U1.5 (A0)
/Power/A1: JP17.1 (A), R4.1, U1.4 (A1)
/Power/ALERT: U1.7 (ALERT)
/Power/BATT_IN: D2.2 (A), J16.2, J16.3, Q1.2 (S), R32.1
/Power/IN+_SENSE: C2.2, J13.2, JP18.1 (A), U1.1 (IN+), U1.2 (IN+), U1.3 (IN+)
/Power/IN-_SENSE: J13.1, U1.14 (IN-), U1.15 (IN-), U1.16 (IN-)
/Power/TERMINAL_IN: J5.2, J16.1
/Power/VIN: C6.1, J8.1, U7.1 (IN), U18.3 (IN+), U18.4 (IN+), U19.3 (IN+), U19.4 (IN+)
/i2c+: R18.2, U1.9 (SCL); also elsewhere on the board
/i2c-: R22.2, U1.8 (SDA); also elsewhere on the board
GND: C1.2, C2.1, C3.2, C6.2, C8.2, C10.2, C11.2, C12.2, C13.2, C14.2, D1.1 (K), D5.1 (K), D10.1 (K), D11.1 (K), J1.1, J1.2, J5.1, J9.2, J9.MP (MountPin), Q1.1 (G), Q2.2 (E), R4.2, R7.2, R33.2, TP12.1, U1.6 (GND), U1.11 (GND), U7.2 (GND), U13.2 (GND), U14.2 (GND), U15.2 (GND), U18.1 (IN-), U18.2 (IN-), U18.7 (OUT-), U18.8 (OUT-), U19.1 (IN-), U19.2 (IN-), U19.7 (OUT-), U19.8 (OUT-); also elsewhere on the board
unnamed: BZ1.1, J10.1, R19.1
unnamed: D1.2 (A), R5.1
unnamed: D5.2 (A), R21.2
unnamed: D10.2 (A), R32.2
unnamed: D11.2 (A), R17.2
unnamed: C11.1, D2.1 (K), D12.1 (A1), J8.2, Q1.3 (D)
unnamed: D12.2 (A2), R33.1
unnamed: JP18.2 (B), U1.12 (VBUS)
unnamed: Q2.1 (B), R20.2
unnamed: BZ1.2, Q2.3 (C), R19.2
unnamed: R21.1, U13.3 (OUT), U14.1 (VDD), U14.3 (EN), U15.3 (OUT)
VOUT_A: TP10.1, U18.5 (OUT+), U18.6 (OUT+); also elsewhere on the board
VOUT_B: C10.1, TP11.1, U13.1 (IN), U15.1 (IN), U19.5 (OUT+), U19.6 (OUT+); also elsewhere on the board

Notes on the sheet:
VOUT_A = 9-10V (DV and Stepper Motors) VOUT_B = 6.5V (ESP, Servos, linerar regulators)
12V Power
5V POWER and ideal diode isolation
6.5v (Supplies ESP, Relays coils, Servos, and linear regulators)
9-12V (DC and Stepper Motors)
alternate RPP
BATTERY IN
High Side Sense (Short if no pwr sense)
Buck Modules for Battery Vin

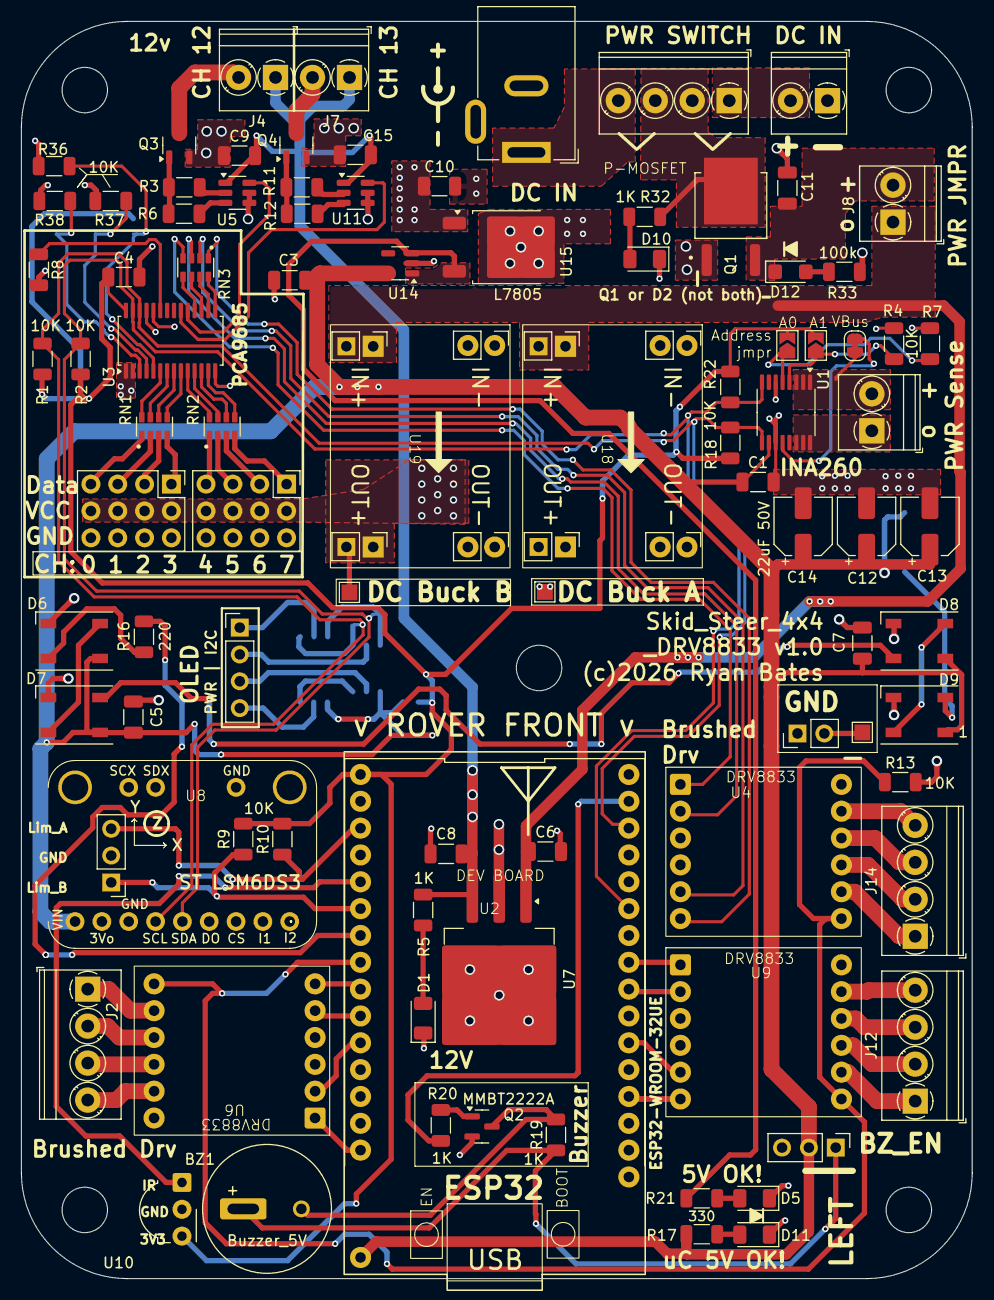
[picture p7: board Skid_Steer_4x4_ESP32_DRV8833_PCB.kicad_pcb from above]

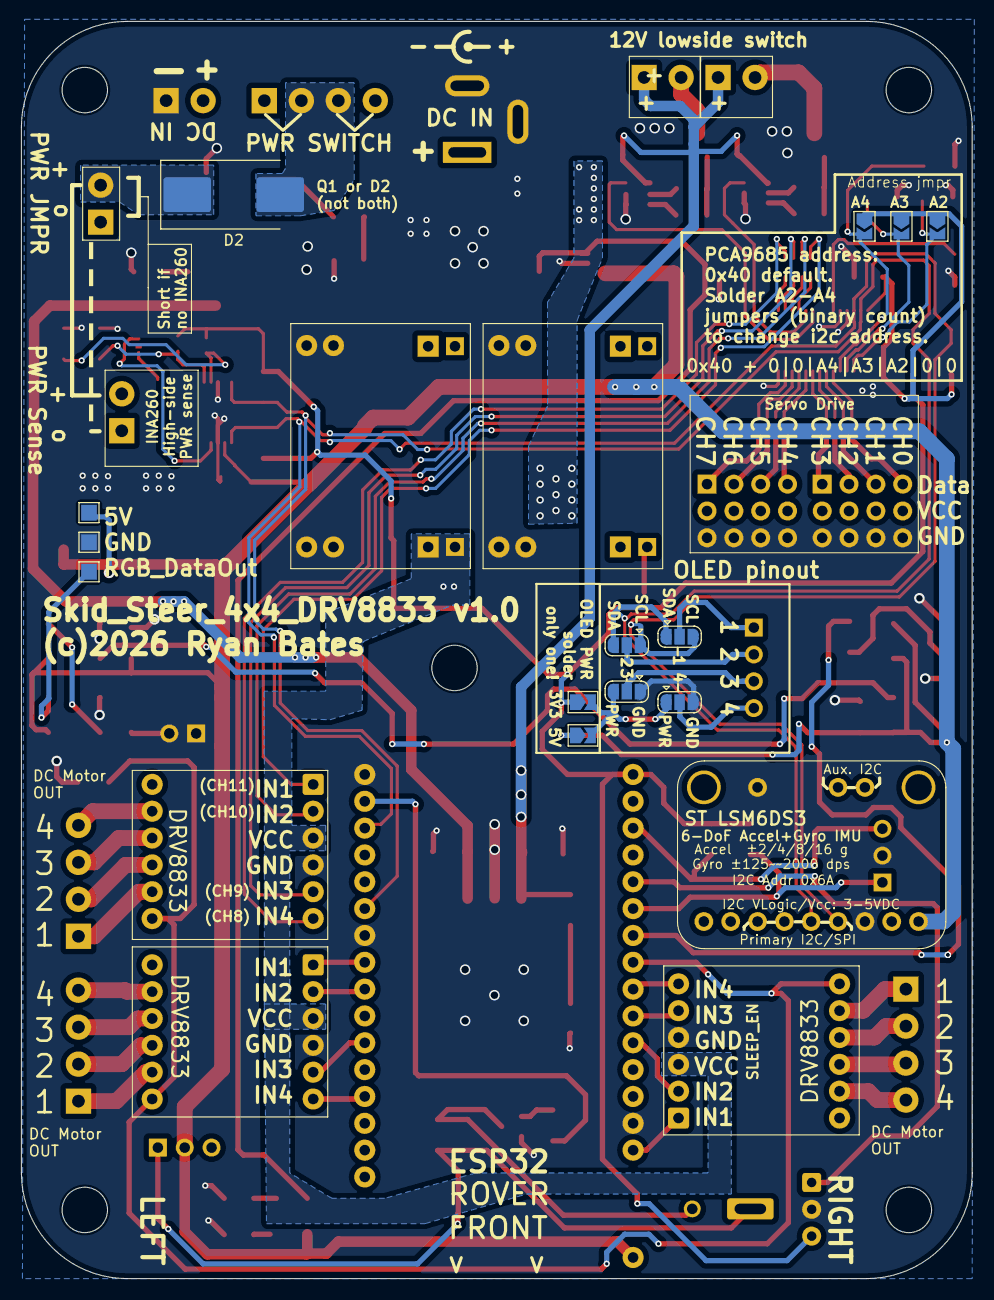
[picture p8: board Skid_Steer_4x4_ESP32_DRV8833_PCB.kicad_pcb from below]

Board: 2 copper layers, 90.0 x 119.0 mm, 111 parts (13 on the bottom side), 101 nets.

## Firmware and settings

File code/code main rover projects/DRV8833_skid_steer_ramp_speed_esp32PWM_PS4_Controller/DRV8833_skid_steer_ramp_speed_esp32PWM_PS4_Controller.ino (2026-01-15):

/*

//DEMO motors, OLED, INA260, 

  Sensor & Output Function
  - Reads battery voltage/current from INA260, prints to OLED
  - Beeps if battery voltage below threshold (16.5V)
  - Reads IMU XYZ acceleration and XYZ Gyroscope, and temperature; prints to Serial
  - Beeps if tilt exceeds 45° for at least 1 second
  - Pairs to PS4 controller, moves motors based on analog Joystick values

ES32-Wroom-32UE (Digikey P/N: 1965-ESP32-DEVKITC-32UE-ND) with classic Bluetooth needed for PS4 controller
   ESP32 Bluetooth MAC 5C:01:3B:63:67:56   //yours will be different!!!!!!!!
   ESP32 wifi: 5C:01:3B:63:67:54           //yours will be different!!!!!!!!



Motor Drivers: DRV8833

Sensor i2c addresses: 
OLED (32x128) 
PCA9685
INA260 


uses the LEDC PWM for ESP32
//you must downgrade the esp32 board package to pre3.0 version for the espPWM to compile
//compiles on v 2.0.17 esp32 by Espressif

 Table 1. H-Bridge Logic (From TI datasheet) https://www.ti.com/lit/ds/symlink/drv8833.pdf

 xIN1 | xIN2 | xOUT1 | xOUT2 |   FUNCTION
 -----------------------------------------
  0   |  0   |   Z   |   Z   | Coast = Fast Decay
  0   |  1   |   L   |   H   | Reverse
  1   |  0   |   H   |   L   | Forward
  1   |  1   |   L   |   L   | Brake = Slow Decay (i cant get this to work irl)
  motors just act like coast/fast decay when all set to H
   
Motor/chassis Layout:

       FRONT
    ___________
  /            \
 │  ◄ L1   R1 ► │
 |              | 
 |              | 
 │  ◄ L2   R2 ► │
 └──────────────┘
       BACK
*/

#include <PS4Controller.h> 
#include <WiFi.h>  // make sure this is included for WiFi.macAddress()
//aside from printing  wifi mac to the oled (for convienence only) initializing this is pointless and 
#include <esp_bt.h> // Include for BT MAC address

int driveDirection = 1;   // 1 = normal, -1 = reversed (drive direction/orientation mode)
#define BUZZER_PIN 23     // piezo buzzer
#define BUZZER_CHANNEL 8   // free LEDC channel (0–15 available, motors already use 0–7)

// Deadzone for joystick
#define DEADZONE 15  

//===IMU setup===
#include <Adafruit_LSM6DS3TRC.h>
#include <math.h>
// ===== Accelerometer/Gyro =====
Adafruit_LSM6DS3TRC lsm6ds3trc;
// ===== Tilt Detection =====
const float TILT_THRESHOLD = 45.0;      // Degrees
const unsigned long TILT_HOLD = 1000;   // 1 second
unsigned long tiltStartTime = 0;


// ==== NeoPixel Strip ====
#include <Adafruit_NeoPixel.h>
#define LED_PIN 13
#define LED_COUNT 4
Adafruit_NeoPixel strip(LED_COUNT, LED_PIN, NEO_GRB + NEO_KHZ800);

// ==== Store speeds for LED update ====
int motorSpeeds[4] = {0, 0, 0, 0};     // Current speed for each motor, used for RGB LEDs

// ===== OLED DISPLAY SETTINGS =====
#include <GyverOLED.h>
GyverOLED<SSD1306_128x32, OLED_NO_BUFFER> oled; // Using 128x32 without buffer

// ===== INA260 SENSOR SETTINGS =====
#include <Adafruit_INA260.h>
#define INA260_ADDRESS 0x45 // set by both solder jumpers
Adafruit_INA260 ina260;

//special constrain (map) for floating numbers. Needed for battery voltage %
float mapFloat(float x, float in_min, float in_max, float out_min, float out_max) {
    return (x - in_min) * (out_max - out_min) / (in_max - in_min) + out_min;
}

// //Speed toggle with R1
// float speedMultiplier = 1.0;   // default high speed
// bool lowSpeedMode = false;     // toggle state

// Motor driver pin assignments (DRV8833)
#define L_MOTOR1_IN1 13   //(Front Left) //was GPIO14, which was a strapping pin :(
#define L_MOTOR1_IN2 27   //(Front Left) 
#define L_MOTOR2_IN1 26   //(Rear Left)  
#define L_MOTOR2_IN2 25   //(Rear Left)  

#define R_MOTOR1_IN1 19   //(Front Right) 
#define R_MOTOR1_IN2 18   //(Front Right) 
#define R_MOTOR2_IN1 17    //(Rear Right)  //was GPIO5, which was a strapping pin :(
#define R_MOTOR2_IN2 4    //(Rear Right)

#define SLEEP_PIN 33      // DRV8833 nSLEEP pin

// PWM settings
#define PWM_FREQ 2000     // 2kHz → still kinda squealy and noisy but performance seems ok
#define PWM_RES  12        // 12-bit resolution → values 0–4095

// Assign LEDC channels
#define CH_L1 0
#define CH_L2 1
#define CH_L3 2
#define CH_L4 3
#define CH_R1 4
#define CH_R2 5
#define CH_R3 6
#define CH_R4 7

unsigned long lastTimeStamp = 0;
int lastLX = 0, lastLY = 0, lastRX = 0, lastRY = 0;

void setup() {

  pinMode(SLEEP_PIN, OUTPUT); // DRV8833 Sleep pin
  digitalWrite(SLEEP_PIN, LOW);  // Start with motor drive disabled

ledcSetup(BUZZER_CHANNEL, 2000, 8);   // 2 kHz, 8-bit resolution
ledcAttachPin(BUZZER_PIN, BUZZER_CHANNEL);

  Serial.begin(115200);
  delay(500);
    // Initialize NeoPixel strip
  strip.begin();
  strip.show();  // LEDs off at start

  // Initialize INA260
  if (!ina260.begin(INA260_ADDRESS)) {
    Serial.println(F("Couldn't find INA260 chip"));
    while (1) delay(10);
  }
  Serial.println(F("Found INA260 chip"));

  // ----- LSM6DS3TR-C init -----
  if (!lsm6ds3trc.begin_I2C()) {
    Serial.println("Failed to find LSM6DS3TR-C chip");
    while (1) delay(10);
  }
  Serial.println("LSM6DS3TR-C Found");
  lsm6ds3trc.configInt1(false, false, true);  // Accel DRDY on INT1
  lsm6ds3trc.configInt2(false, true, false);  // Gyro DRDY on INT2

  // Initialize OLED
  oled.init(); oled.clear();
  oled.flipH(true);  // true = flip horizontally, false = normal
  oled.flipV(true);  // true = flip horizontally, false = normal
  oled.setScale(2);       // 1–4 (4 = huge text)
  oled.invertText(false);
  oled.setCursorXY(0, 0);
  oled.print(F("Ready"));
  oled.update();
  delay(1000); // wait for reading the screen

  oled.setScale(1);       // 1–4 (4 = huge text)
  oled.clear();

 // Serial Print Wifi and Bluetooth MAC
  uint8_t baseMac[6];
  esp_read_mac(baseMac, ESP_MAC_BT); // Get the Bluetooth MAC address
  Serial.print("Bluetooth MAC: ");
  for (int i = 0; i < 5; i++) {
    Serial.printf("%02X:", baseMac[i]);
  }
  Serial.printf("%02X\n", baseMac[5]);
/////Wifi mac
  Serial.print("Wifi MAC: ");
  Serial.println(WiFi.macAddress());

  // OLED Print Bluetooth MAC
  oled.setCursorXY(0, 0);
  oled.print(F("BT MAC:"));
  oled.setCursorXY(0, 8); // move down 8 pixels
    // Convert to string
  char BTmacStr[18];
  sprintf(BTmacStr, "%02X:%02X:%02X:%02X:%02X:%02X",
          baseMac[0], baseMac[1], baseMac[2],
          baseMac[3], baseMac[4], baseMac[5]);
  oled.print(BTmacStr);

  // OLED Print WiFi MAC
  oled.setCursorXY(0, 16); // next line
  oled.print(F("WiFi MAC:"));
  oled.setCursorXY(0, 24); // next line
  oled.print(WiFi.macAddress());
  oled.update();
  delay(2000); // wait for reading the screen
  oled.clear(); //final clear before main loop

  PS4.begin("5C:01:3B:63:67:54");
  PS4.attach(notify);
  PS4.attachOnConnect(onConnect);
  PS4.attachOnDisconnect(onDisConnect);

  // Setup PWM channels
  ledcSetup(CH_L1, PWM_FREQ, PWM_RES);
  ledcSetup(CH_L2, PWM_FREQ, PWM_RES);
  ledcSetup(CH_L3, PWM_FREQ, PWM_RES);
  ledcSetup(CH_L4, PWM_FREQ, PWM_RES);

  ledcSetup(CH_R1, PWM_FREQ, PWM_RES);
  ledcSetup(CH_R2, PWM_FREQ, PWM_RES);
  ledcSetup(CH_R3, PWM_FREQ, PWM_RES);
  ledcSetup(CH_R4, PWM_FREQ, PWM_RES);

  // Attach channels to pins
  ledcAttachPin(L_MOTOR1_IN1, CH_L1);
  ledcAttachPin(L_MOTOR1_IN2, CH_L2);
  ledcAttachPin(L_MOTOR2_IN1, CH_L3);
  ledcAttachPin(L_MOTOR2_IN2, CH_L4);

  ledcAttachPin(R_MOTOR1_IN1, CH_R1);
  ledcAttachPin(R_MOTOR1_IN2, CH_R2);
  ledcAttachPin(R_MOTOR2_IN1, CH_R3);
  ledcAttachPin(R_MOTOR2_IN2, CH_R4);

  // Sleep pin
  pinMode(SLEEP_PIN, OUTPUT);
  digitalWrite(SLEEP_PIN, LOW);  // Start in low-power mode
}
//==LOOP START=========================================================================================
void loop() {
  delay(100);
  displayDashboard();
  IMU_read();
  
}

// 🟡 Apply deadzone to joystick input
int applyDeadzone(int value) {
  return (abs(value) < DEADZONE) ? 0 : value;
}

//==============Buzzer square wave generation--------------
void buzzerTone(int freq, int duty = 128) {
  ledcWriteTone(BUZZER_CHANNEL, freq);  // set frequency
  ledcWrite(BUZZER_CHANNEL, duty);      // 50% duty cycle by default
}

void buzzerOff() {
  ledcWrite(BUZZER_CHANNEL, 0);         // turn off 
}

void notify() { //do stuff when controller input is detected 
  if (millis() - lastTimeStamp > 50) {
    int lxRaw = PS4.LStickX();
    int lyRaw = PS4.LStickY();
    int rxRaw = PS4.RStickX();
    int ryRaw = PS4.RStickY();

    int lx = applyDeadzone(lxRaw);
    int ly = applyDeadzone(lyRaw);
    int rx = applyDeadzone(rxRaw);
    int ry = applyDeadzone(ryRaw);

    if (lx != lastLX || ly != lastLY || rx != lastRX || ry != lastRY) {
      Serial.println("Joystick Movement:");
      Serial.printf("  LStick: X=%d, Y=%d\n", lx, ly);
      Serial.printf("  RStick: X=%d, Y=%d\n", rx, ry);
      lastLX = lx;
      lastLY = ly;
      lastRX = rx;
      lastRY = ry;
    }

// Toggle speed mode when R1 is pressed
// if (PS4.R1()) {
//   lowSpeedMode = !lowSpeedMode;
//   speedMultiplier = lowSpeedMode ? 0.5 : 1.0;  // half speed in low mode
//   Serial.printf("Speed Mode: %s\n", lowSpeedMode ? "LOW" : "HIGH");
//   delay(200); // simple debounce so it doesn’t toggle too fast
//                }
// 🟡 Toggle horn
if (PS4.Square()) {
    buzzerTone(740);   // 740Hz beep (this is F#)
} else {
    buzzerOff();
}

// 🟡 Toggle drive orientation with Cross button
if (PS4.Triangle()) {
    driveDirection *= -1;  // flip between 1 and -1
    Serial.printf("Drive Direction: %s\n", (driveDirection == 1) ? "Normal" : "Reversed");
    delay(200); // debounce
}


// 🟢 Control motors
// Scale joystick -127..127 to motor PWM -255..255
int forward = map(ly, -127, 127, -255, 255);  
int turn    = map(rx, -127, 127, -255, 255);

// forward *= speedMultiplier; //speed controller with R1 toggle
// turn    *= speedMultiplier;

// apply drive direction toggle 
forward *= driveDirection;
turn    *= driveDirection;


int leftSpeed  = constrain(forward + turn, -255, 255);
int rightSpeed = constrain(forward - turn, -255, 255);


    // Scale 8-bit joystick range (-255..255) to 12-bit PWM (0..4095)
    setMotor(CH_L1, CH_L2, leftSpeed);
    setMotor(CH_L3, CH_L4, leftSpeed);
    setMotor(CH_R1, CH_R2, rightSpeed);
    setMotor(CH_R3, CH_R4, rightSpeed);

  // Assign speeds for LED updates
    motorSpeeds[0] = leftSpeed;   // L1
    motorSpeeds[1] = leftSpeed;   // L2
    motorSpeeds[2] = rightSpeed;  // R1
    motorSpeeds[3] = rightSpeed;  // R2
updateMotorLEDs();
   
    lastTimeStamp = millis();
  }


}

// 🟢 DRV8833 motor control function using LEDC PWM
void setMotor(int ch_in1, int ch_in2, int speed) {
  int pwmVal = map(abs(speed), 0, 255, 0, (1 << PWM_RES) - 1);

  if (speed > 0) {
    ledcWrite(ch_in1, pwmVal);
    ledcWrite(ch_in2, 0);
  } else if (speed < 0) {
    ledcWrite(ch_in1, 0);
    ledcWrite(ch_in2, pwmVal);
  } else {
    ledcWrite(ch_in1, 0);
    ledcWrite(ch_in2, 0);
  }
}

// PS4 events
void onConnect() {
  Serial.println("Connected!");
  digitalWrite(SLEEP_PIN, HIGH);  // Wake DRV8833
}

void onDisConnect() {
  Serial.println("Disconnected!");
  digitalWrite(SLEEP_PIN, LOW);   // Sleep DRV8833
}

//======================subroutines=================================================================
// Update all LEDs based on motorSpeeds array, then show the strip
void updateMotorLEDs() {
  for (int i = 0; i < LED_COUNT; i++) {
    int absSpeed = abs(motorSpeeds[i]);
    int brightness = map(absSpeed, 0, 255, 0, 50); // scale brightness for full PWM range

    if (motorSpeeds[i] > 0) {
      strip.setPixelColor(i, strip.Color(0, brightness, 0));   // Green forward
    } 
    else if (motorSpeeds[i] < 0) {
      strip.setPixelColor(i, strip.Color(0, brightness / 5, brightness)); // Blue reverse
    } 
    else {
      strip.setPixelColor(i, strip.Color(20, 0, 0));   // Red stopped/coast
    }
  }
  strip.show();
}
// get data and print to the OLED
void displayDashboard() {
  // 1️⃣ PS4 controller battery %
  int batteryPercent = PS4.Battery(); //this reading +/-10% accruate ?
  oled.setCursorXY(0, 0);
  oled.setScale(1); 
  oled.print(F("PS4: "));
  oled.print(batteryPercent);
  oled.print(F("%   ")); // extra spaces to erase old digits

  // 2️⃣ Bus voltage
  float voltage_V = ina260.readBusVoltage() / 1000.0; //convert from mV to V
  //float batteryVoltage = abs((voltage_V-16.5) / (20.4 - 16.5) *100); //M18 charge level. smart but unsigned values lets the % wrap around
  float batteryVoltage = constrain(mapFloat(voltage_V, 16.5, 20.4, 0.0, 100.0), 0.0f, 100.0f); //battery charge level

  oled.setCursorXY(0, 12);
  oled.print(F("Bat: "));
  oled.print(voltage_V, 1); 
  oled.print(F("V   ")); 
  oled.setCursorXY(72, 12);
   oled.print(F("(")); 
  oled.print(batteryVoltage, 0);
  oled.print(F("%) "));

  // 3️⃣ Current
  float current_A = abs(ina260.readCurrent() / 1000.0); //sometimes its -0.0 which is dumb
  oled.setCursorXY(0, 24);
  oled.print(F("Cur: "));
  oled.print(current_A, 1);
  oled.print(F("A  "));

//  //Speed: High or Low
//  oled.setCursorXY(110, 0);
//  oled.print(lowSpeedMode ? "Lo " : "Hi");

// 4️⃣ Drive Direction indicator
  oled.setCursorXY(110, 12);  // bottom-right corner
  oled.print(driveDirection == 1 ? "Fwd " : "Rev ");

  oled.update();
}

//=== IMU math and sensor get====
void IMU_read(){
  // ----- Read LSM6DS3TR-C -----
  sensors_event_t accel, gyro, temp;
  lsm6ds3trc.getEvent(&accel, &gyro, &temp);
  float ax = accel.acceleration.x;
  float ay = accel.acceleration.y;
  float az = accel.acceleration.z;
  float tempC = temp.temperature; 
  float tempF = ((tempC * 9/5) + 32) ;
  // Print accelerometer values to Serial
  //Serial.printf("Accel X: %.3f m/s², Y: %.3f m/s², Z: %.3f m/s²\n", ax, ay, az);
  //Calculate the vector magnitue in 3 dimensions (X,Y,Z). so regardless of direction, we can calculate 
//if the 4x4 rover is at a tilt
  float magnitude = sqrt(ax*ax + ay*ay + az*az);
  float tilt_deg = acos(az / magnitude) * (180.0 / PI);
  //float pitch = atan2(ax, sqrt(ay*ay + az*az)) * 180.0 / PI; //not sure about this
  //float roll  = atan2(ay, sqrt(ax*ax + az*az)) * 180.0 / PI; //unsure


  //Serial.printf("Tilt: %.1f°\n", tilt_deg);
 oled.setCursorXY(66,0); 
 oled.print(F("Angle:")); //print angle in degrees ( no degee sign in oled library)
 oled.print(tilt_deg, 0);
 oled.print(F("  ")); // Clear leftover chars
 //oled.print(F("X:"));
 //oled.print(pitch, 0);

 oled.setCursorXY(75, 24);
 oled.print(F("Tf: "));
 oled.print(tempF, 1);
}

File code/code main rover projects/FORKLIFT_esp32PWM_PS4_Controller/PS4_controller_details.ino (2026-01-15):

/*
| Button / Control           | Type             | Range or Values           | Function Call                |
| -------------------------- | ---------------- | ------------------------- | ---------------------------- |
| **Cross (X)**              | Digital          | `true` / `false`          | `PS4.Cross()`                |
| **Circle (O)**             | Digital          | `true` / `false`          | `PS4.Circle()`               |
| **Square (☐)**             | Digital          | `true` / `false`          | `PS4.Square()`               |
| **Triangle (△)**           | Digital          | `true` / `false`          | `PS4.Triangle()`             |
| **Up (D-Pad)**             | Digital          | `true` / `false`          | `PS4.Up()`                   |
| **Down (D-Pad)**           | Digital          | `true` / `false`          | `PS4.Down()`                 |
| **Left (D-Pad)**           | Digital          | `true` / `false`          | `PS4.Left()`                 |
| **Right (D-Pad)**          | Digital          | `true` / `false`          | `PS4.Right()`                |
| **L1**                     | Digital          | `true` / `false`          | `PS4.L1()`                   |
| **R1**                     | Digital          | `true` / `false`          | `PS4.R1()`                   |
| **L2**                     | Analog + Digital | 0–255 or `true` / `false` | `PS4.L2Value()` / `PS4.L2()` |
| **R2**                     | Analog + Digital | 0–255 or `true` / `false` | `PS4.R2Value()` / `PS4.R2()` |
| **L3 (Left Stick Click)**  | Digital          | `true` / `false`          | `PS4.L3()`                   |
| **R3 (Right Stick Click)** | Digital          | `true` / `false`          | `PS4.R3()`                   |
| **Share**                  | Digital          | `true` / `false`          | `PS4.Share()`                |
| **Options**                | Digital          | `true` / `false`          | `PS4.Options()`              |
| **PS (Logo)**              | Digital          | `true` / `false`          | `PS4.PS()`                   |
| **Touchpad Press**         | Digital          | `true` / `false`          | `PS4.Touchpad()`             |

| Stick Axis        | Type   | Range           | Function Call   |
| ----------------- | ------ | --------------- | --------------- |
| **Left Stick X**  | Analog | `-127` to `127` | `PS4.LStickX()` |
| **Left Stick Y**  | Analog | `-127` to `127` | `PS4.LStickY()` |
| **Right Stick X** | Analog | `-127` to `127` | `PS4.RStickX()` |
| **Right Stick Y** | Analog | `-127` to `127` | `PS4.RStickY()` |

| Info              | Type    | Range/Values | Function Call       |
| ----------------- | ------- | ------------ | ------------------- |
| **Battery Level** | Analog  | `0–100` (%)  | `PS4.Battery()`     |
| **Connected?**    | Digital | `true/false` | `PS4.isConnected()` |

*/

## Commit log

2025-12-20 Update vendor link for Motor 12V, 82 RPM
    Added an alternative vendor link for the 12V motor.
2026-01-09 Add PLA Filament cost to hardware list
2026-01-11 Revise electronics BoM with cost details
    Updated the electronics Bill of Materials (BoM) to include line total costs and a total cost summary.
2026-01-11 Update README with PCB features and cost adjustments
    Added details about PCB capabilities and updated total costs.
2026-01-11 Enhance README with GIF and PCB details
    Added GIF and expanded description of PCB functionality.
2026-01-12 Enhance README with CAD link and images
    Updated README to include CAD project link and additional images.
2026-01-12 Update CAD project link with account info
    Added note about creating a free onShape account for exporting and downloading the CAD project.
2026-01-12 Add linear actuator link to README
    Added a link for the linear actuator used in the forklift build.
2026-01-13 Add optional forklift assembly motors and parts list
2026-01-13 Fix formatting of resistor list in README.md
2026-01-14 Revise optional forklift assembly parts list
    Updated the list of optional forklift assembly motors and parts, including new items and adjustments to existing entries.
2026-01-15 Update CAD project description for clarity
2026-01-15 Update resistor list in README.md
2026-01-15 kiCAD files
    [ESP32-WROOM-32 GPIO Reference.ods, Power.kicad_sch, Skid_Steer_4x4_ESP32_DRV8833_PCB.kicad_pcb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]

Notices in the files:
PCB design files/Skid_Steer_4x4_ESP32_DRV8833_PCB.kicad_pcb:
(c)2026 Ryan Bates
